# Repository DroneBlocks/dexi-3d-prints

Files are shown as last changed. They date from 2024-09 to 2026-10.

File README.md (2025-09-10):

# DEXI Drone 3D Printed Parts

Collection of 3D printable components for DEXI drone builds and AVR competition kits.

## Structure

### AVR Compute Kit Parts
Competition-ready parts for AVR teams:
- **New Teams/**: Complete kit for first-time participants
- **Returning Teams/**: Essential parts for experienced teams  
- **Replacement Guards/**: Prop guard replacements

Key components:
- ARK Flow cases (top/bottom)
- Camera mounts and LED rings
- Landing gear system (mount, brace, foot)
- Mount rods and Raspberry Pi plate
- Battery holder

### DEXI-5 Platform
Custom drone platform components:
- Landing gear (2" and 3" variants)
- Camera mounts (tilted, downward)
- IR LED and receiver mounts
- Front laser mounts
- GPS and databot mounts
- Battery tray and ring systems

### DEXI-10 Platform
- X500 LED mount system

### Accessories
- **AVR2024 Laser Cup**: Competition target component
- **Pi Camera Wrench**: Tool for camera nut adjustment

## Print Settings
- Layer height: 0.2mm recommended
- Infill: 15-20% for structural parts
- Supports: Required for overhangs

## Usage
All STL files are print-ready. Check commit history for latest updates and modifications.

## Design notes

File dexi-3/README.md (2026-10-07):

# DEXI 3

## MicoAir flow sensor case

`DEXI 3 MicoAir Flow Case Top.step` and `DEXI 3 MicoAir Flow Case Bottom.step` hold the MicoAir flow sensor.

`DEXI 3 MicoAir Flow Mount 90 Degrees Rotated.step` is the same mount rotated 90 degrees, a safer option for cable routing.

**Note:** to mount this flow sensor, replace the 20 mm standoffs with 15 mm standoffs.

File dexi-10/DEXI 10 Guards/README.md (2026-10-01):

# DEXI 10 Guards

Prop guard parts for the DEXI 10.

| File | Part |
|---|---|
| `DEXI 10 Guard Top.step` | Top guard piece |
| `DEXI 10 Guard Bottom.step` | Bottom guard piece |
| `DEXI 10 Guard Coupler.step` | Connects the guard pieces at each motor arm |
| `DEXI 10 AVR Guard Adapter.step` | Lets existing AVR guards be fitted to the DEXI 10 |

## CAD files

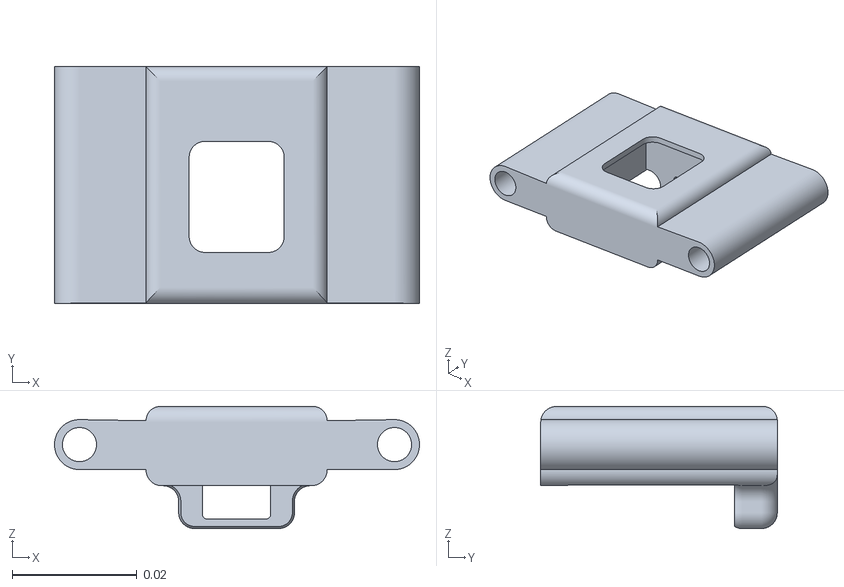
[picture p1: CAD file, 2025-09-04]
AVR Compute Kit Parts/New Teams/AVR Camera Mount.stl
0.0585 x 0.0379 x 0.0196

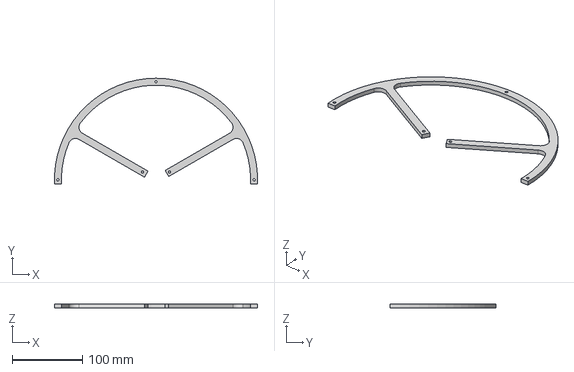
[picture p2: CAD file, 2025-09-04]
AVR Compute Kit Parts/Replacement Guards Files/AVR Prop Guard Bottom.step
289.2 x 150.4 x 5.00 mm

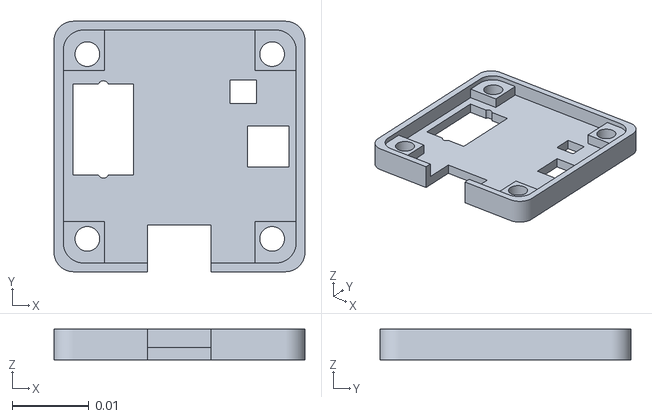
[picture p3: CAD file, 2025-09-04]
AVR Compute Kit Parts/Returning Teams/AVR Ark Flow Top Case.stl
0.0326 x 0.0325 x 0.00401

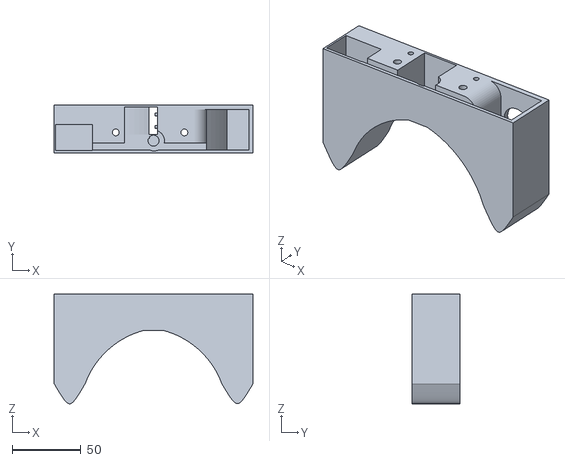
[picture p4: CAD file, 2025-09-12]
avr/AVR_2024_Sphero_Hit_Block_Hole_For_Green_Light.stl
145.0 x 35.0 x 79.9

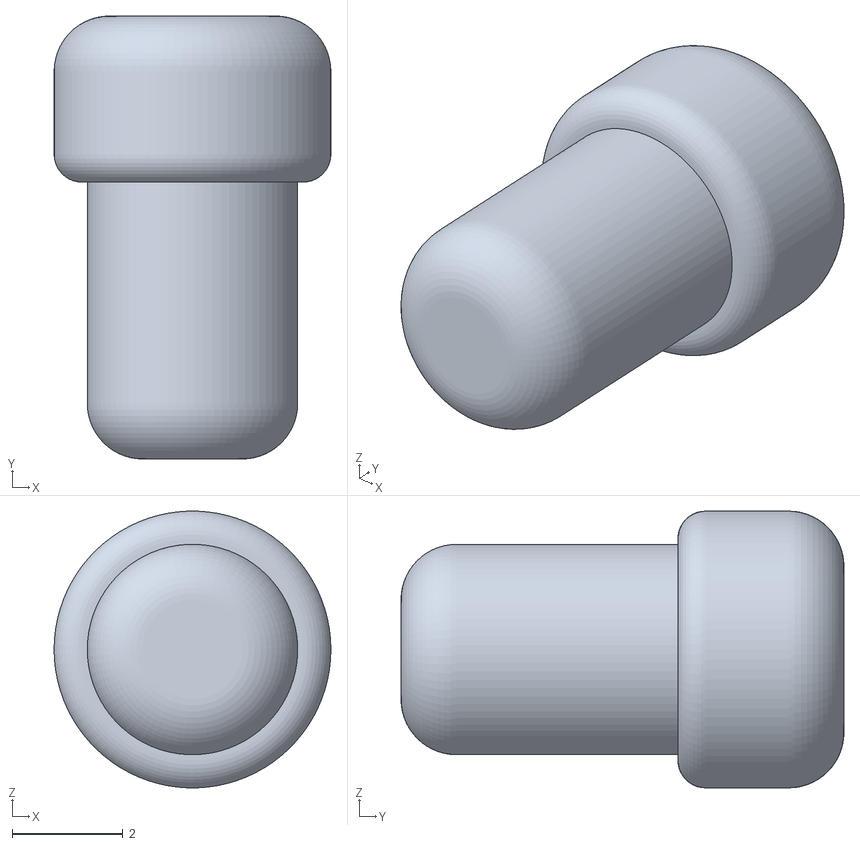
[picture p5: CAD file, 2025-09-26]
compute-kit/hailo_fastener.stl
5.00 x 8.00 x 5.00

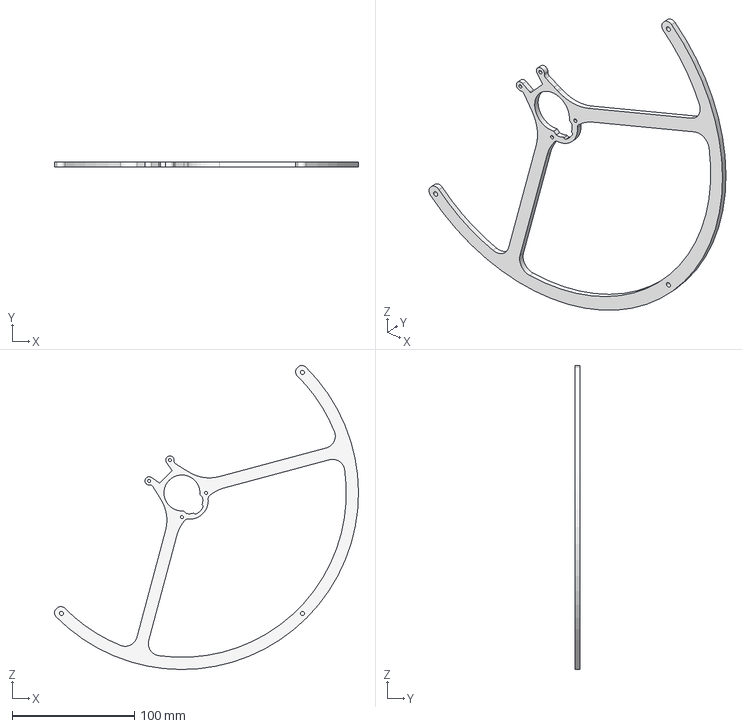
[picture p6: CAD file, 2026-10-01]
dexi-10/DEXI 10 Guards/DEXI 10 Guard Bottom.step
249.1 x 3.81 x 249.1 mm

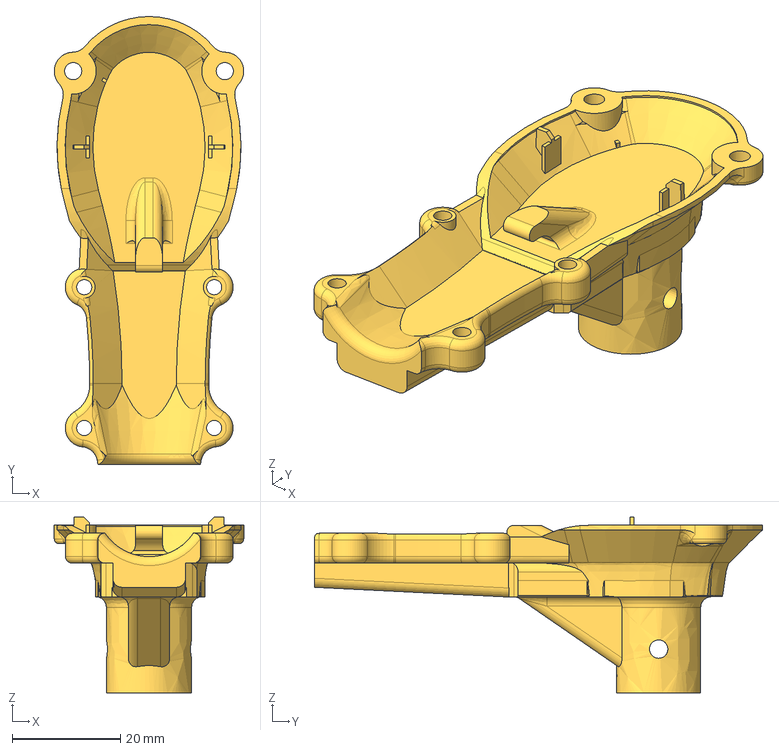
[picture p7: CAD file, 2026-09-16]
dexi-10/DEXI 10 Landing Gear Mount.step
35.0 x 82.7 x 32.5 mm

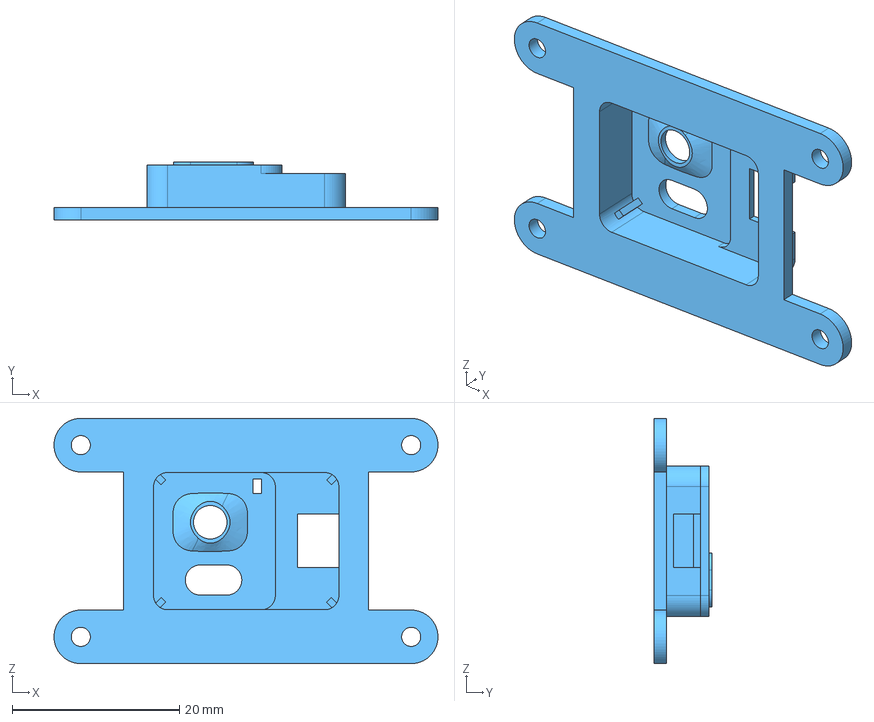
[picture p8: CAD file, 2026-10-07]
dexi-3/DEXI 3 MicoAir Flow Mount 90 Degrees Rotated.step
45.9 x 6.96 x 29.3 mm

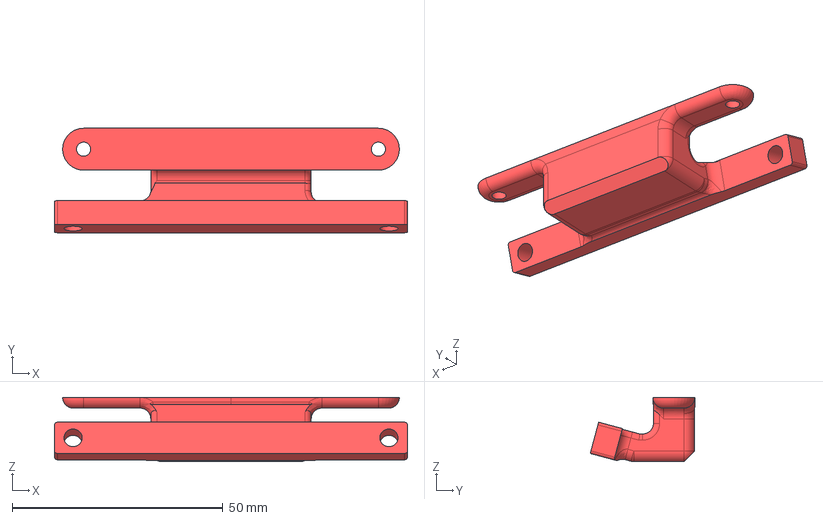
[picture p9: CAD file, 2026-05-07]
dexi-5/DEXI 5 Oka D-Lite 15 Degree Mount.step
83.8 x 24.8 x 15.2 mm

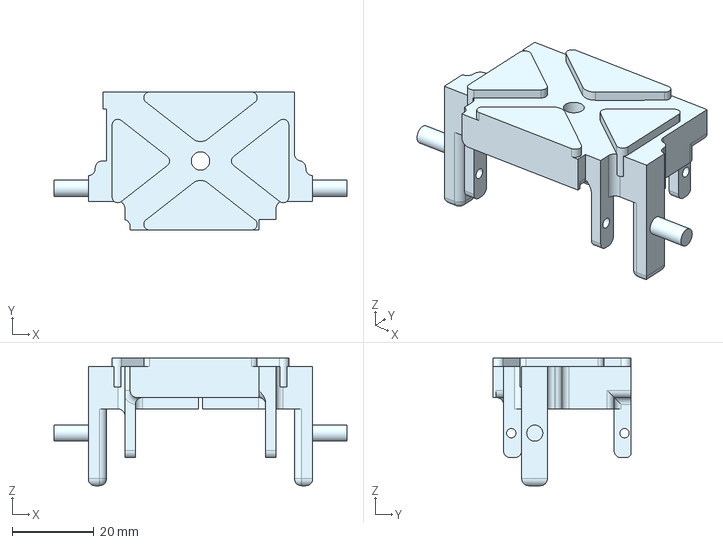
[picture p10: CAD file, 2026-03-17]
dexi-claw-mechanism/DEXI Claw Holder.step
71.7 x 33.7 x 31.2 mm

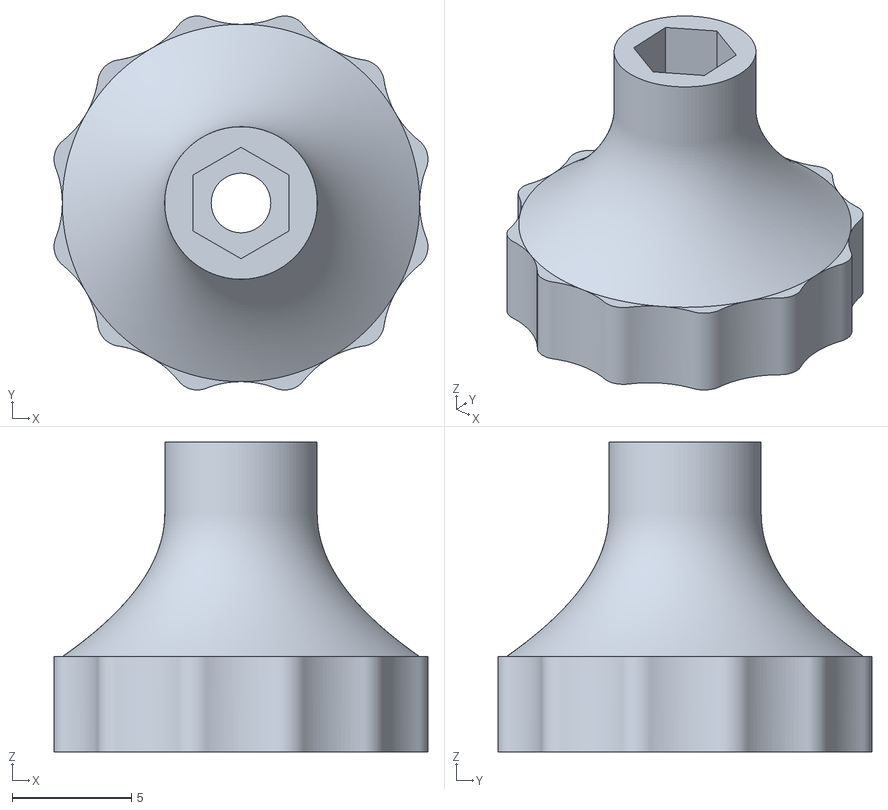
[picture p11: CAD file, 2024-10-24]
pi_camera_wrench.stl
15.7 x 15.7 x 13.0

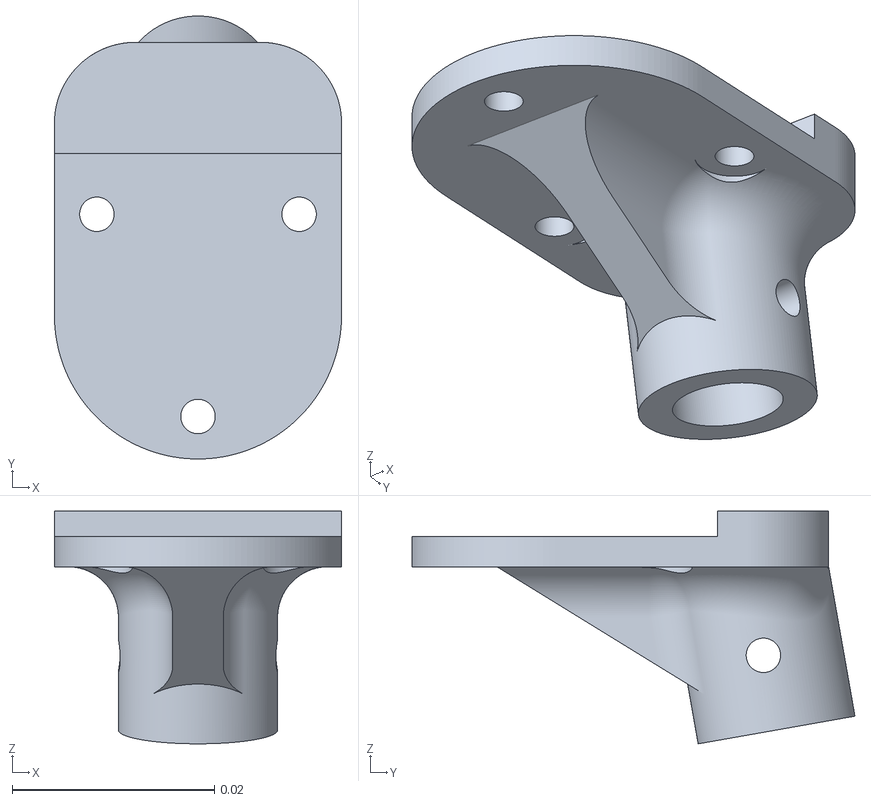
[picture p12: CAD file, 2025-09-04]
AVR Compute Kit Parts/New Teams/AVR Landing Gear Mount.stl
0.0284 x 0.0438 x 0.023

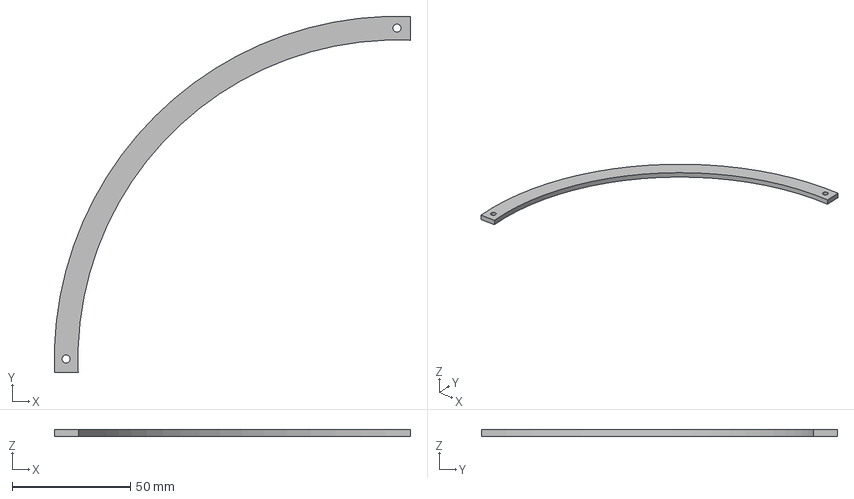
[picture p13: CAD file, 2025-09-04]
AVR Compute Kit Parts/Replacement Guards Files/AVR Prop Guard Top Flat.step
150.3 x 150.3 x 3.00 mm

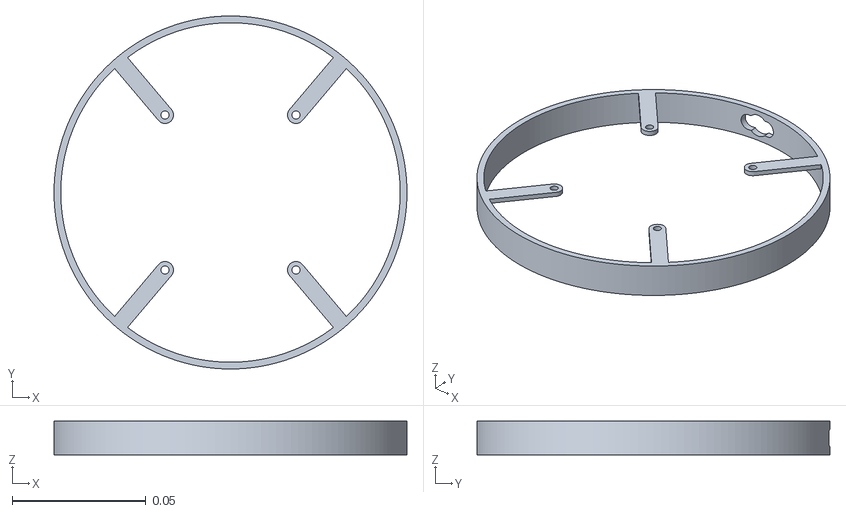
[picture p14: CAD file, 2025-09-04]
AVR Compute Kit Parts/Returning Teams/AVR LED Ring.stl
0.132 x 0.132 x 0.0127

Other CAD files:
avr/AVR2024_LaserCup.stl
dexi-10/DEXI 10 Guards/DEXI 10 Guard Top.step
dexi-10/DEXI 10 Landing Gear Foot.step
dexi-3/DEXI 3 MicoAir Flow Case Top.step
AVR Compute Kit Parts/New Teams/AVR Ark Flow Bottom Case.stl
AVR Compute Kit Parts/New Teams/AVR Battery Holder.stl
AVR Compute Kit Parts/New Teams/AVR Landing Gear Brace.stl
AVR Compute Kit Parts/New Teams/AVR Landing Gear Foot.stl
AVR Compute Kit Parts/New Teams/AVR Left Mount Rod.stl
AVR Compute Kit Parts/New Teams/AVR Pi Plate.stl
AVR Compute Kit Parts/New Teams/AVR Right Mount Rod.stl
AVR Compute Kit Parts/Replacement Guards Files/AVR Prop Guard Bottom.stl
AVR Compute Kit Parts/Replacement Guards Files/AVR Prop Guard Top Flat.stl
AVR Compute Kit Parts/Returning Teams/AVR Ark Flow Bottom Case.stl
AVR Compute Kit Parts/Returning Teams/AVR Left Mount Rod.stl
AVR Compute Kit Parts/Returning Teams/AVR Right Mount Rod.stl
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

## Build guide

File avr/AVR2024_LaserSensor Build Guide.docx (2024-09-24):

The 2024 Advanced Vertical Robotics (AVR) competition will equip the DEXI done with an onboard laser that competitors will use to shoot at targets. This guide will show competitors how to re-create the real target that they will face for the competition. This document will show you the exact parts you will need, and a real code snippet sample from the field control system that you can use to flash to an Arduino and simulate your challenge.

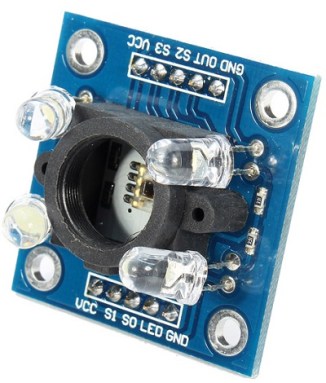
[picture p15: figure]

We will use this commercial off the shelf part. The TCS3200 is a color sensor. It uses a TAOS RGB sensor. An array of photodiodes that conduct electricity based on the color it sees and a current to frequency converter to generate a square wave to be interpreted by the Arduino. It also has 4 white lights designed to illuminate the object the sensor is looking at.

These lights are not needed in this use context. You may optionally bend them out of the way or remove them entirely. On the 2024 AVR courts the LEDs will be left in place and bent out of the way.

With that brief tech talk out the way let’s look at the build.

What you will need:

Part | QTY | Seller | Suggested Links
TCS3200 Color Sensor | 1 | Amazon | https://a.co/d/7dAYYYL
Brass M3 Threads | 4 | Amazon | https://a.co/d/3EnqoOf
M3 10mm Bolts | 4 | Amazon | https://a.co/d/72mEKN0
PLA+ (white) | 1 | Amazon | https://a.co/d/20TKjVD
Light Diffuser. | 1 | Home Depot | https://www.homedepot.com/p/Westek-Ultra-Thin-LED-White-Puck-Light-2-Pack-BL-PUTN-W2T/315068101

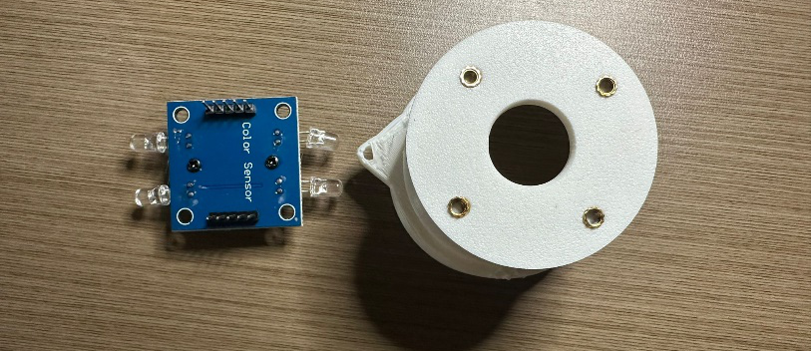
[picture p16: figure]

Step 1: Print out the laser cup. Use the attached STL. Depending on the tolerance of the material and the printer you use, you may need to use a finishing tool to make the laser hole a few mm wider to accept the sensor housing.

Step 2: Add the brass threads. I bent the LEDs on the light senor back and to the side to get them out of the way. Then pressed the black sensor housing to mark the screw hole locations with a pencil. Use a soldering iron to heat press the threads into place.

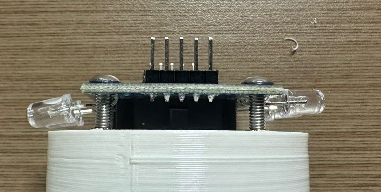
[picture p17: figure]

Step 3: Connect the sensor to the cup using 4 M3 bolts. 1 per corner.

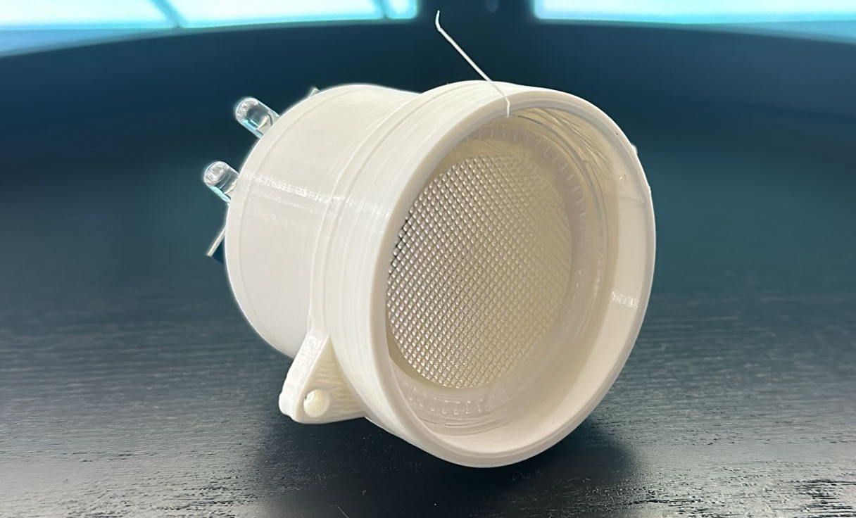
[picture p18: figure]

Step 5: Disassemble the light pucks to harvest the refractor lens. Place a bead of hot glue around the ledge inside the printed frame and lay in the lens. The concave end must face the outside and the convex end must face the sensor.

Step 6: Connect the sensor to your microcontroller using the following recommended pins for use with the sample code. You may do this however you like. We recommend you use Dupont connectors for simplicity.

TCS3200 Pins | Arduino Pins
SC0 | 5
SC1 | 6
SC2 | 8
SC3 | 7
OUT | 9
VCC | 5V
GND | GND

Step 7: Flash the “laserBench” INO script to your Arduino. No libraries required.

Step 8: Monitor the output. The program will print only when it registers a hit. Note: you must be precise when firing lasers.

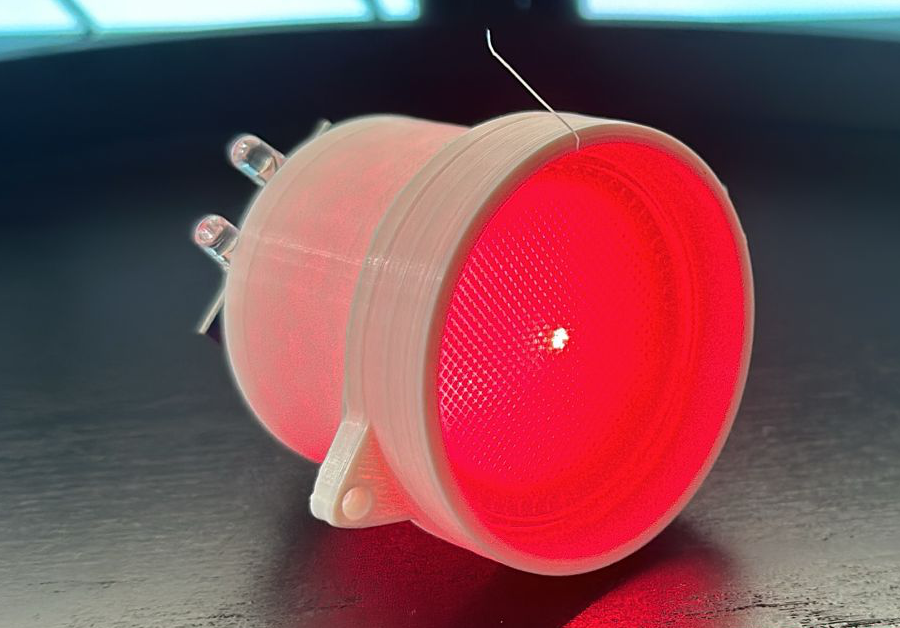
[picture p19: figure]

Step 9: Practice shooting. The sensitivity and debouncing will be set as with what you are testing in this guide.

Best of luck!

AutoInvent Inc. 2024

AVR 2024 Laser Sensor Build Guide

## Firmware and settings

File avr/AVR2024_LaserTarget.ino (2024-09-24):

//Pin definitions for Sensor 1
#define S0_1 5
#define S1_1 6
#define S2_1 8
#define S3_1 7
#define OUT_1 9

// Pin definitions for Sensor 2
// #define S0_2 10
// #define S1_2 11
// #define S2_2 12
// #define S3_2 13
// #define OUT_2 14
#define S0_2 A4
#define S1_2 A3
#define S2_2 A1
#define S3_2 A0
#define OUT_2 A2



//Variables for debouncing and sensitivity
int debounceDelay = 500;         
int sensitivityThreshold = 90; //Using 10 or 90 here for testing


void setup() 
{
  pinMode(S0_1, OUTPUT);
  pinMode(S1_1, OUTPUT);
  pinMode(S2_1, OUTPUT);
  pinMode(S3_1, OUTPUT);
  pinMode(OUT_1, INPUT);

  pinMode(S0_2, OUTPUT);
  pinMode(S1_2, OUTPUT);
  pinMode(S2_2, OUTPUT);
  pinMode(S3_2, OUTPUT);
  pinMode(OUT_2, INPUT);

  //Set frequency scaling to 20%
  digitalWrite(S0_1, HIGH);
  digitalWrite(S1_1, LOW);

  digitalWrite(S0_2, HIGH);
  digitalWrite(S1_2, LOW);

  Serial.begin(9600);
}

void loop() 
{
  int redFrequency_1 = readRedColor(S2_1, S3_1, OUT_1);
  if (redFrequency_1 < sensitivityThreshold) 
  {
    Serial.println("Sensor 1: Red");
  }
  else 
  {
    //Serial.println("Sensor 1: Not Red");
  }

 
  int redFrequency_2 = readRedColor(S2_2, S3_2, OUT_2);
  if (redFrequency_2 < sensitivityThreshold) 
  {
    Serial.println("Sensor 2: Red");
  } 
  else 
  {
    //Serial.println("Sensor 2: Not Red");
  }

  delay(debounceDelay);
}

//Function to read the red component from a TCS230 sensor
int readRedColor(int S2, int S3, int OUT) 
{
  digitalWrite(S2, LOW);
  digitalWrite(S3, LOW);

  int redFrequency = pulseIn(OUT, LOW);
  return redFrequency;
}

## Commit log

2024-05-07 v1 3D prints
    [DEXI Battery Tray.stl, DEXI Camera Tilted.stl, DEXI Landing Gear Talon.stl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]
2024-08-27 2" landing gear
    [DEXI_landing_gear_2_inch_front_left_rear_right.stl, DEXI_landing_gear_2_inch_front_right_rear_left.stl]
2024-08-28 DEXI Infrared led receiver and laser mount
    [DEXI_ir_led_mount_bottom.stl, DEXI_ir_led_mount_top.stl]
2024-09-09 Rename 2"
    [DEXI_landing_gear_2_inch.stl, DEXI_landing_gear_2_inch_mirrored.stl]
2024-09-09 Add 3" gear
    [DEXI_landing_gear_3_inch.stl, DEXI_landing_gear_3_inch_mirrored.stl]
2024-09-12 Front laser mounts
2024-09-18 Rear infrared receiver mounts
2024-09-24 Laser target for AVR 2024
    [AVR2024_LaserCup.stl]
2024-09-24 Laser target build guide
2024-09-24 Laser target Arduino code
2024-10-24 Wrench for pi camera nuts
    [pi_camera_wrench.stl]
2024-12-20 Added mounting holes for 2mm screws
    [DEXI_ARK_GPS_mount_left.stl, DEXI_ARK_GPS_mount_right.stl]
2025-04-15 LED mount WIP
    [dexi_10_x500_led_mount.stl]
2025-09-04 Upload new 3d files for compute kit
    Upload new 3d files for compute kit
    [AVR Ark Flow Bottom Case.stl, AVR Ark Flow Top Case.stl, AVR Battery Holder.stl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]
2025-09-04 AVR Compute Kit Parts
    [AVR Ark Flow Bottom Case.stl, AVR Ark Flow Top Case.stl, AVR Battery Holder.stl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]
2025-09-26 M.2 Fastener prototype
    [hailo_fastener.stl]
2026-01-10 Quentin DEXI-3 prototype
    [quentin_dexi-3_bottom_plate.stl, quentin_dexi-3_top_plate.stl]
2026-02-05 Create DEXI 10 H-Flow Mount.step
    [DEXI 10 H-Flow Mount.step]
2026-03-14 Add DEXI Claw mechanism STEP files
    [DEXI Claw Holder.step, DEXI Claw.step, DEXI Servo Claw.step]
2026-03-24 Add DEXI 3 final parts (2m version)
    [DEXI 3 Flow Mount Top V3.step]
2026-05-07 Add new DEXI 3 and DEXI 5 3D print parts
    - dexi-5: Oka D-Lite 15 Degree Mount, Oka D-Lite Mount Forward
    - dexi-3/2m DEXI 3 And parts (final): Battery Case V2, XT30 Mount V4, Flow Case V4
    [DEXI 3 Battery Case V2.step, DEXI 3 Flow Case V4.step, DEXI 3 XT30 Mount V4.step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]
2026-05-07 Add Oka D-Lite mounts to dexi-10
    - DEXI 10 Oka D-Lite Forward mount.stl
    - DEXI 5 Oka D-Lite 15 Degree Mount.stl
    [DEXI 10 Oka D-Lite Forward mount.stl, DEXI 5 Oka D-Lite 15 Degree Mount.stl]
2026-05-07 Add DEXI 10 Oka D-Lite mounts to dexi-10
    - DEXI 10 Oka D-Lite 15 Degree Mount.stl
    - DEXI 10 Oka D-Lite Forward Mount.stl
    [DEXI 10 Oka D-Lite 15 Degree Mount.stl, DEXI 10 Oka D-Lite Forward Mount.stl]
2026-06-11 Replace dexi-3 folder with final 3D printed parts
    [DEXI 3 Antenna Mount.step, DEXI 3 Battery Case V2.step, DEXI 3 Battery Case.step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]
